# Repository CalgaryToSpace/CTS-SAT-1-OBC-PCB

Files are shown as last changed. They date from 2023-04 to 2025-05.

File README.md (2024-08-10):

# CTS-SAT-1-OBC-PCB

This is the design repository for the CTS-SAT-1 ("FrontierSat") onboard computer (OBC) PCB.

This OBC is host to an STM32 and several flash chips, and interfaces with all other electrical components on the 3U CubeSat.

## PCB Stackup

This PCB uses the [JLCPCB `JLC04161H-2116A` stackup](https://jlcpcb.com/impedance). It is a 6-layer, impedance-controlled PCB.

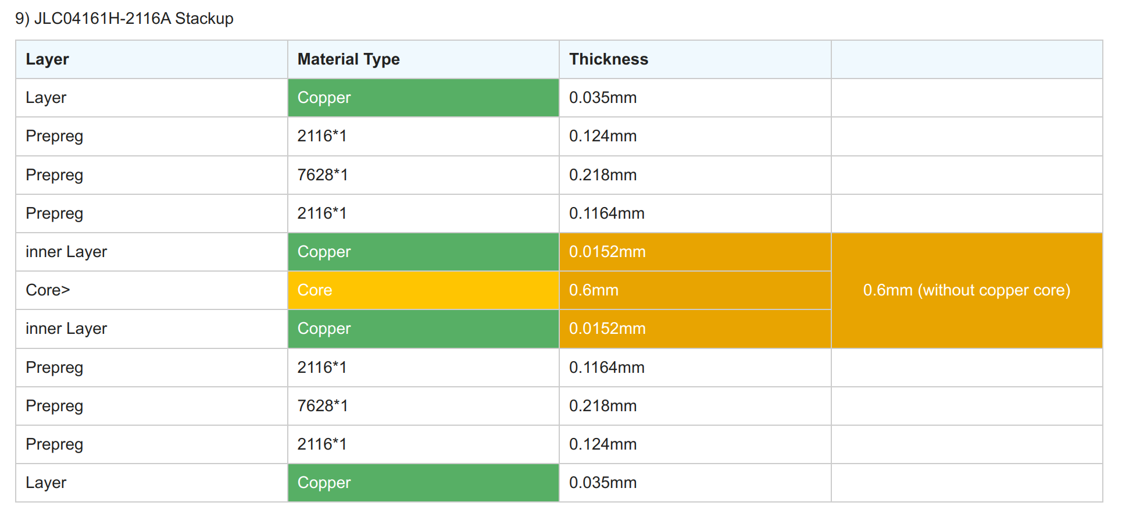
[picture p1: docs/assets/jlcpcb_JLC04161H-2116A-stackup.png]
JLC04161H-2116A Layer Stackup Table Screenshot


## Electrical Wire Comments

It is important to consider the outgassing characteristics of all wires used, so PTFE insulation has been chosen as the standard insulation material. The recommended part number is 5853 BK005, and the maximum recommended current is 1 amp per conductor.

If constructing Space Grade PCBs, use Rogers material as it has low outgassing properties.

## Repository Contents

* OBC PCB
* STM32CubeIDE Pinout/IOC configuration
* Unused early-stage umbilical connection board

## Contributors

* James Chen (contact chen.james2015@gmail.com with any questions)
* Others

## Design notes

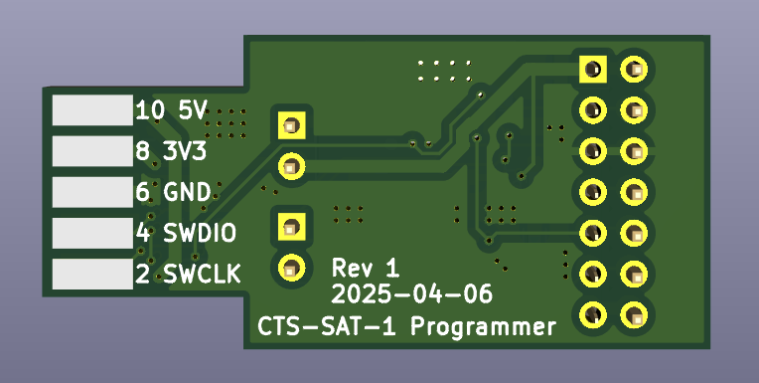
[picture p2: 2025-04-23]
Supplemental_PCBs/Programming_Connector_Adapter_PCB/Render_Bottom.png

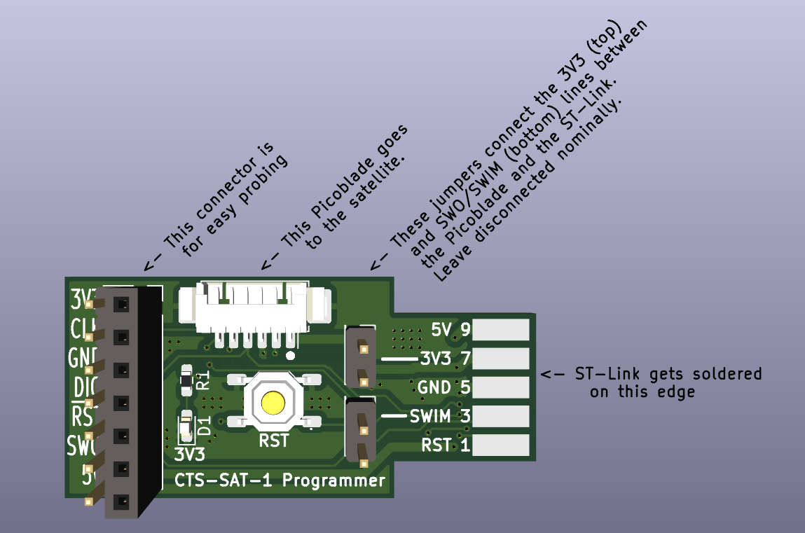
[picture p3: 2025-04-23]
Supplemental_PCBs/Programming_Connector_Adapter_PCB/Render_Top.png

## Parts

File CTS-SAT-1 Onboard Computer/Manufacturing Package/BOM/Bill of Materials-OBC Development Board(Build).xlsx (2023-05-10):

Designator | Description | Quantity | Distributor | Distributor Part # | Manufacturer | Manufacturer Part #
*1, *2, *3, *4 |  | 4
C1, C3, C4, C5, C6, C7, C8, C9, C10, C14, C15, C16, C17, C18, C19, C22, C23, C24, C25, C26, C27, C28, C29, C30, C32, C51, C53 | 0.1 µF ±10% 25V Ceramic Capacitor X7R 0603 (1608 Metric) | 27 | Digikey | 1276-1006-1-ND | Samsung Electro-Mechanics | CL10B104KA8NNNC
C2, C31 | CAP CER 1UF 25V X7R 0603 | 2 | Digikey | 311-1802-1-ND | Yageo | CC0603KRX7R8BB105
C11, C13, C48, C49, C50 | 4.7 µF Molded Tantalum Capacitors 20 V 1206 (3216 Metric) 4Ohm | 5 | Digikey | 478-1668-1-ND | AVX Corporation | TAJA475K020RNJ
C12, C20 | CAP CER 0.1UF 25V X7R 0402 | 2 | Digikey | 13-CC0402KPX7R8BB104CT-ND | YAGEO | CC0402KPX7R8BB104
C21 | 15 pF ±1% 50V Ceramic Capacitor C0G, NP0 0402 (1005 Metric) | 1 | Digikey | 311-1642-1-ND | YAGEO | CC0402FRNPO9BN150
C33 | CAP TANT 22UF 10% 10V 1206 | 1 | Digikey | 478-11193-1-ND | KYOCERA AVX | TPSA226K010T0900
C34, C35, C36 | CAP ALUM POLY 47UF 20% 25V SMD | 3 | Digikey | P16513CT-ND | Panasonic Electronic Components | 25SVPF47M
C39, C44 | CAP CER 4.7UF 16V X7R 0603 | 2 | Digikey | 490-GRM188Z71C475KE21JCT-ND | Murata Electronics | GRM188Z71C475KE21J
C42, C45, C47 | CAP CER 100PF 50V X7R 0603 | 3 | Digikey | 311-3601-1-ND | YAGEO | CC0603KRX7R9BB101
C43, C46 | CAP CER 33PF 50V X7R 0603 | 2 | Digikey | 399-C0603C330K5RAC7867CT-ND | KEMET | C0603C330K5RAC7867
C52 | CAP CER 10000PF 50V X7R 0603 | 1 | Digikey | 1276-1009-1-ND | Samsung Electro-Mechanics | CL10B103KB8NNNC
D1, D2, D3, D4, D5, D6 | Red 620nm LED Indication - Discrete 2.2V 0603 _1608 Metric | 6 | Digikey | SML-D12U1WT86CT-ND | Rohm Semiconductor | SML-D12U1WT86
D7 | DIODE SCHOTTKY 40V 5A SMC | 1 | Digikey | B540C-FDICT-ND | Diodes Incorporated | B540C-13-F
J3, J8 | CONN HEADER SMD R/A 8POS 1.25MM | 2 | Digi-Key | WM7626CT-ND
J4 | CONN HEADER SMD R/A 4POS 1.25MM | 1 | Digi-Key | WM7622CT-ND
J5, J6 | CONN SOCKET 52POS 0.1 GOLD PCB | 2 | Digikey | SAM11114-ND | Samtec Inc. | ESQ-126-14-G-D
J7, J9, J11 | CONN HEADER SMD R/A 6POS 1.25MM | 3 | Digi-Key | WM7624CT-ND
J10, J13 | CONN HEADER VERT 10POS 1.25MM | 2 | Digikey | WM1739-ND | Molex | 0530471010
J12 | Connector Header Surface Mount, Right Angle 14 position 0.049 (1.25mm) | 1 | Digikey | 900-0532617014CT-ND | Molex | 0532617014
J14, J16, J17, J18, J20 | CONN MCX RCPT STR 50 OHM PCB | 5 | Digikey | ACX1262-ND | Amphenol RF | 252105
L1 | FIXED IND 6.8UH 8A 23.3 MOHM SMD | 1 | Digikey | 541-1303-1-ND | Vishay Dale | IHLP4040DZER6R8M01
R1, R2, R3 | 220 Ohms ±0.5% 0.063W, 1/16W Chip Resistor 0603 (1608 Metric) - Thin Film | 3 | Digikey | RR08P220DCT-ND | Susumu | RR0816P-221-D
R4, R5, R6, R7, R13, R14, R15, R16, R17, R22, R24, R26, R27, R28, R30, R31, R32, R33, R34, R35, R36, R37, R38, R41, R42, R43, R44, R45, R46, R47, R51, R52, R53, R55, R63, R64, R67 | 0 Ohms Jumper 0.1W, 1/10W Chip Resistor 0603 (1608 Metric) Automotive AEC-Q200 Thick Film | 37 | Digikey | RMCF0603ZT0R00CT-ND | Stackpole Electronics Inc | RMCF0603ZT0R00
R8, R11 | RES SMD 1K OHM 1% 1/16W 0603 | 2 | Digikey | A102226CT-ND | TE Connectivity Passive Product | CPF0603F1K0C1
R9, R10, R12, R18, R21, R23, R25, R29, R39, R40, R48, R50, R56, R57, R58, R59, R107, R109 | 22 Ohms ±0.5% 0.063W, 1/16W Chip Resistor 0603 (1608 Metric) - Thin Film | 18 | Digikey | RR08Q22DCT-ND | Susumu | RR0816Q-220-D
R19, R20, R49, R54, R91, R92 | RES SMD 4.7K OHM 1% 1/10W 0603 | 6 | Digikey | CR0603-FX-4701ELFCT-ND | Bourns Inc. | CR0603-FX-4701ELF
R60, R61, R65, R66, R117, R118, R119, R120, R124, R125, R126, R127, R128, R129, R136 | RES 10K OHM 1% 1/8W 0603, 10 kOhms ±0.1% 0.063W, 1/16W Chip Resistor 0603 (1608 Metric) - Thin Film | 15 | Digikey | RNCP0603FTD10K0CT-ND, A119886CT-ND | Stackpole Electronics Inc, TE Connectivity Passive Product | RNCP0603FTD10K0, CPF0603B10KE
R62 | RES 0.5 OHM 1% 1W 2010 | 1 | Digikey | 541-10112-1-ND | Vishay Dale | WSLT2010R5000FEA18
R130, R131 | RES SMD 100 OHM 0.5% 1/16W 0603 | 2 | Digikey | RR08P100DCT-ND | Susumu | RR08P100DCT-ND
R134, R135 | RES 220 OHM 5% 1/16W 0402 | 2 | Digikey | 311-220JRCT-ND | Yageo | RC0402JR-07220RL
TP1, TP2 | Test Point | 2
U1 | IC MCU 32BIT 2MB FLASH 144LQFP | 1 | Mouser |  | STMicroelectronics | STM32L4R5ZIT6
U2, U3, U5, U6 | IC FLASH 1GBIT SPI/QUAD 16SOIC | 4 | Digikey | 1274-1092-ND | Cypress Semiconductor | S70FL01GSAGMFI011
U4 | IC REG BUCK ADJUSTABLE 3A 8SOIC | 1 | Digikey | 505-ADP2303ARDZ-ND | Analog Devices Inc. | ADP2303ARDZ
U7, U8 | IC FRAM 8MBIT SPI 40MHZ 8GQFN | 2 | Digikey | 428-4723-ND | Cypress Semiconductor | CY15B108QN-40LPXI
U9 | IC TRNSLTR BIDIRECTIONAL 14TSSOP | 1 | Digikey | MAX3378EEUD+TCT-ND | Maxim Integrated | MAX3378EEUD+T
U10 | IC TRANSCEIVER FULL 1/1 14SOIC | 1 | Digikey | MAX3086EESD+TCT-ND | Maxim Integrated Products | MAX3086EESD+T
U11, U12 | LORA-E5 WIRELESS MODULE (TAPE RE | 2 | Digikey | 1597-317990829CT-ND | Seeed Technology Co., Ltd | 317990829
U13 | IC RF SWITCH SPDT 3GHZ 6MLPD | 1 | Digikey |  | Skyworks Solutions Inc. | SKY13323-378LF
U14 | IC INVERT SCHMITT 1CH 1IN SC70 | 1 | Digikey
Y1 | XTAL OSC TCXO 20.0000MHZ CSWV | 1 | Digikey | 114-TG2520SMN20.0000M-MCGNNM3CT-ND | EPSON | TG2520SMN 20.0000M-MCGNNM3
Y2 | XTAL OSC TCXO 32.7680KHZ CMOS | 1 | Digikey | SER4422CT-ND | EPSON | TG-3541CE 32.7680KXB3

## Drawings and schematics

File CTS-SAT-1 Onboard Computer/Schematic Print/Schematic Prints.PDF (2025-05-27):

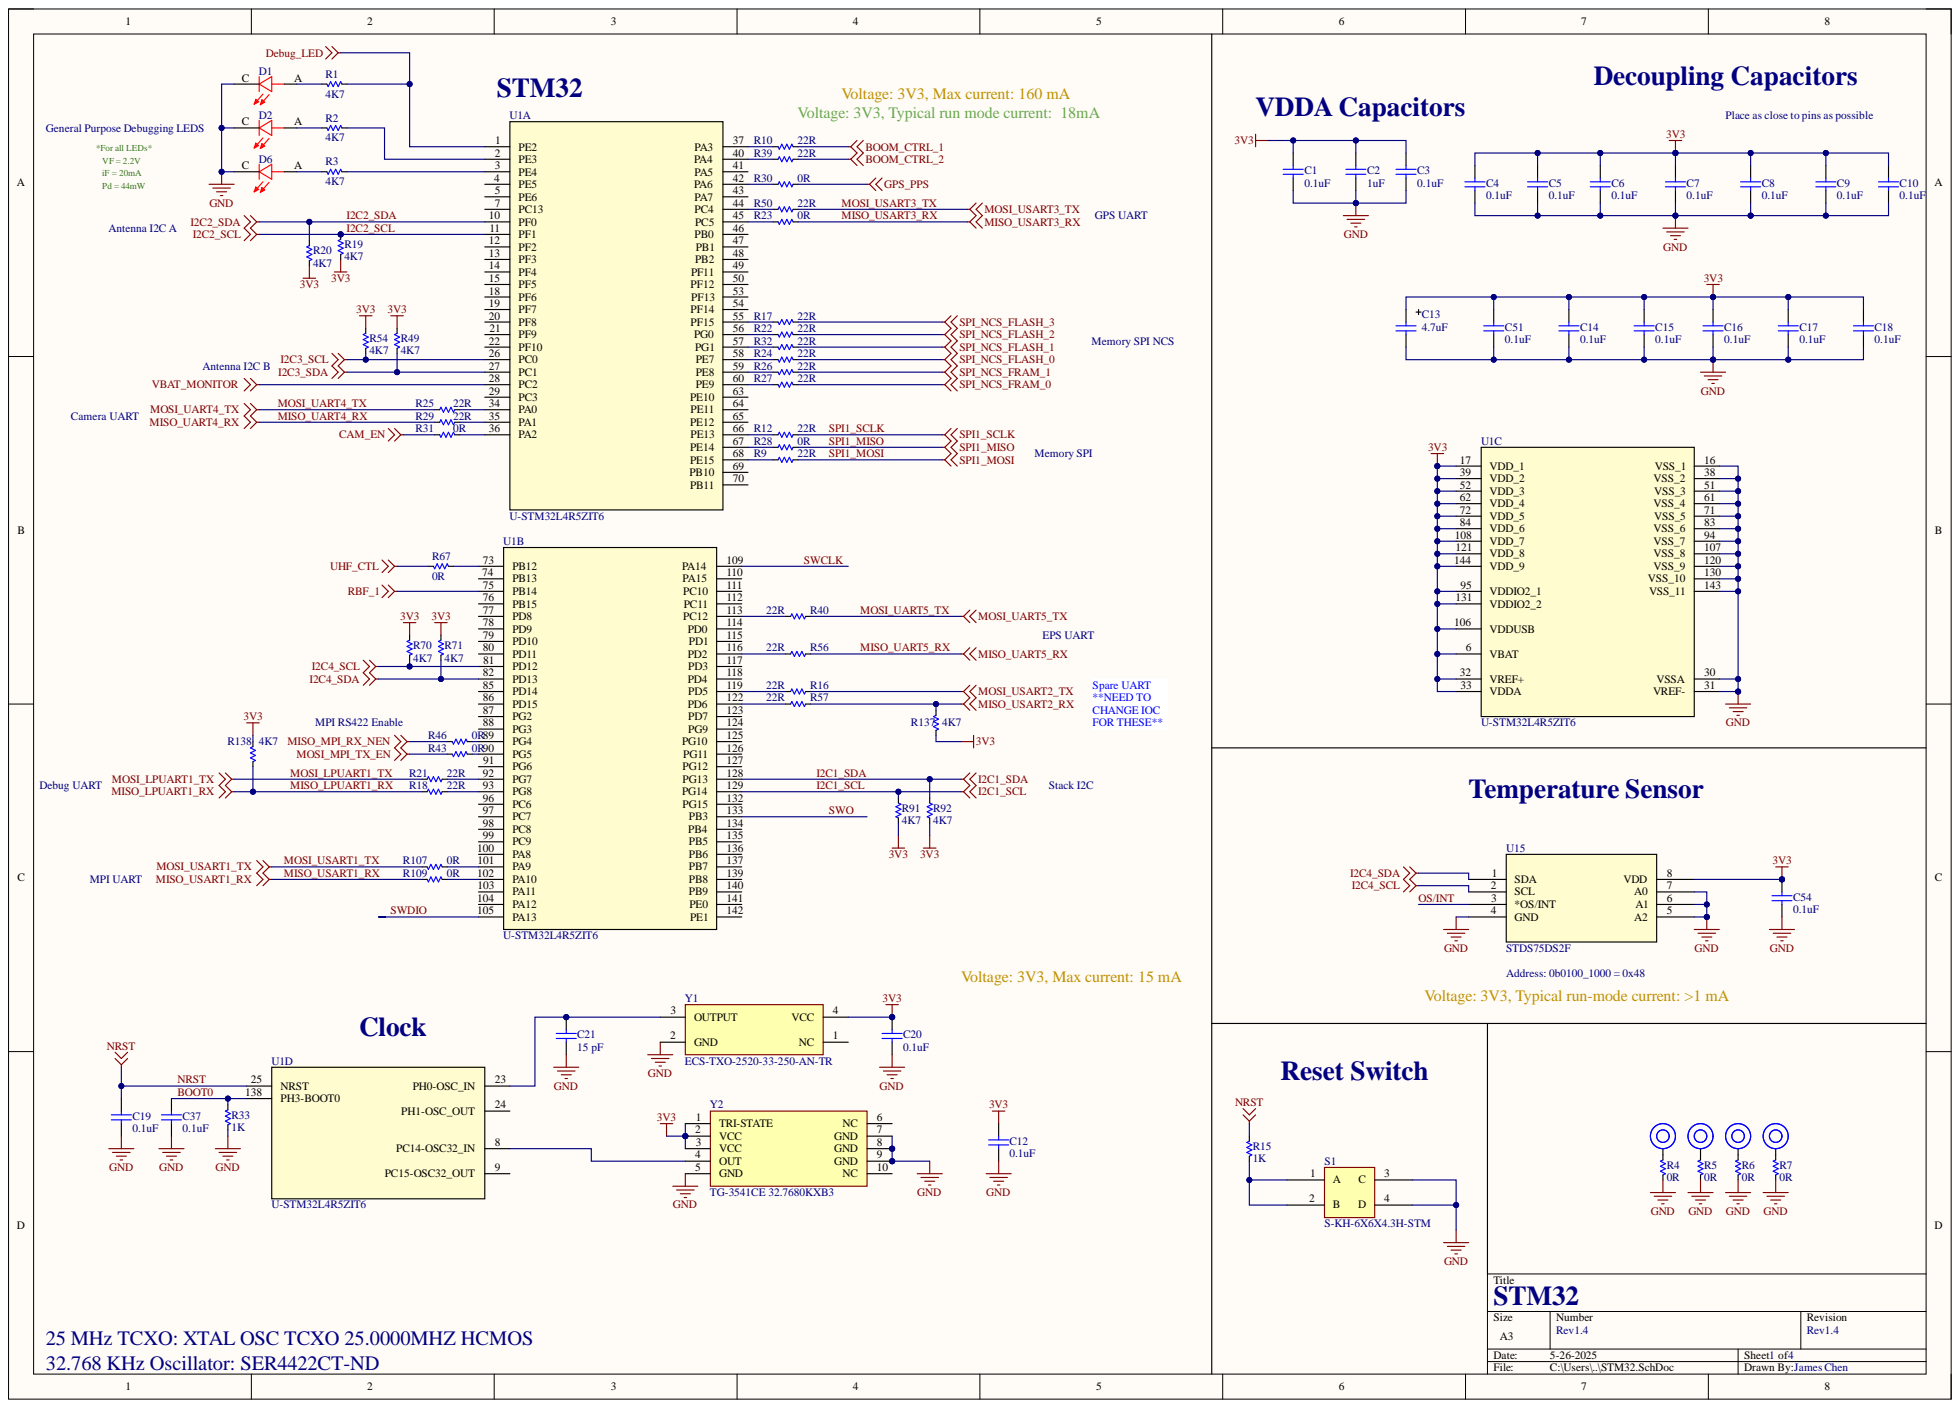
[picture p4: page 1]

Voltage: 3V3, Max current: 160 mA

Voltage: 3V3, Typical run mode current: 18mA

General Purpose Debugging LEDS

Voltage: 3V3, Max current: 15 mA

Voltage: 3V3, Typical run-mode current: >1 mA

ECS-TXO-2520-33-250-AN-TR

BOOT0 | PH3-BOOT0 138

25 MHz TCXO: XTAL OSC TCXO 25.0000MHZ HCMOS
32.768 KHz Oscillator: SER4422CT-ND

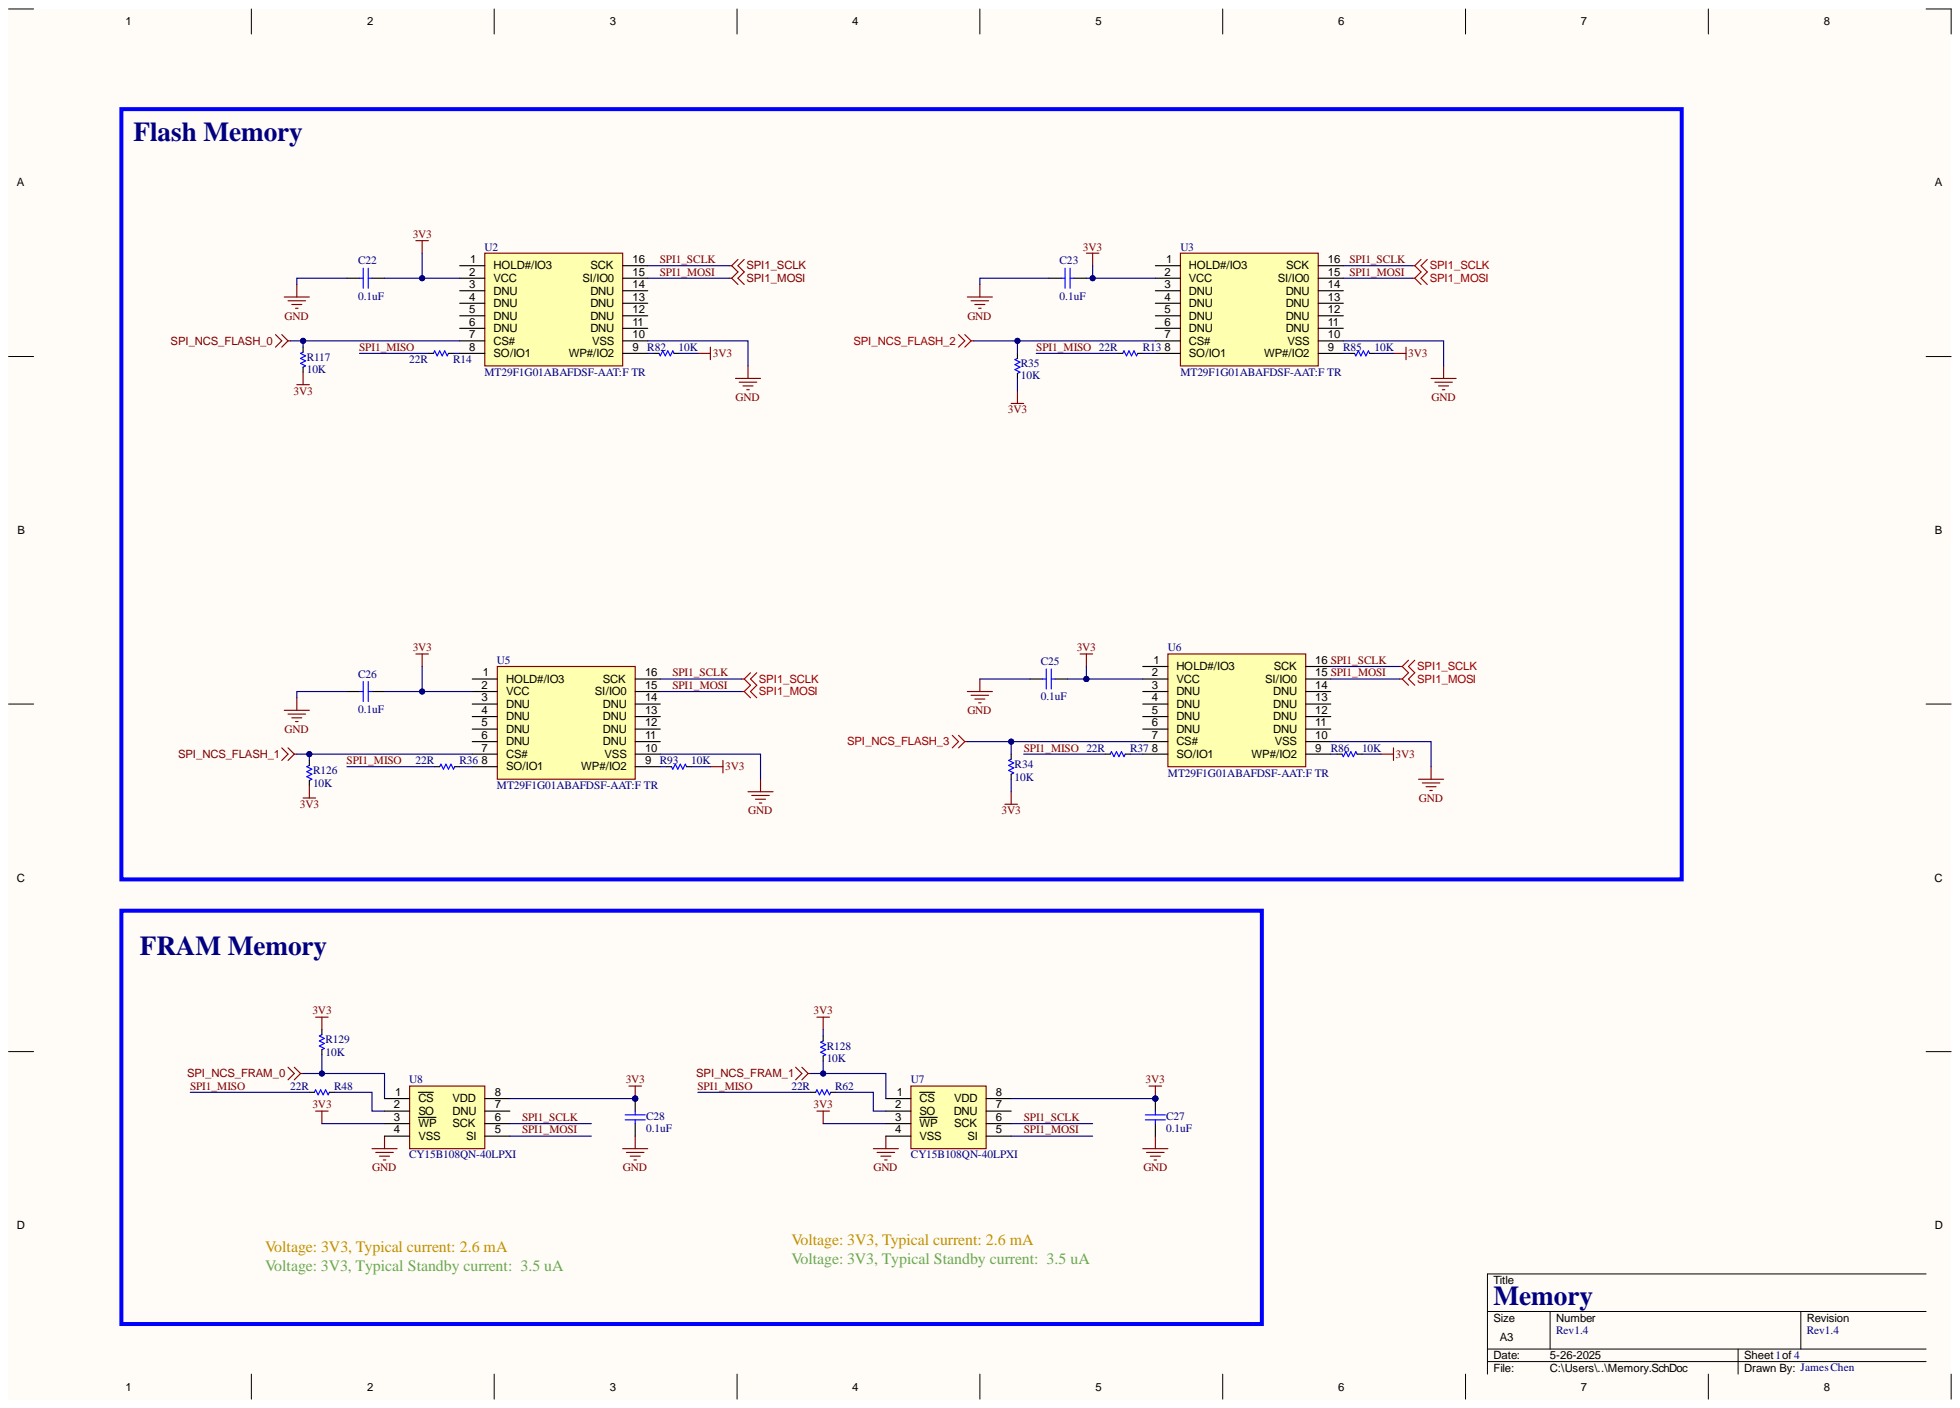
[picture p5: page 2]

Voltage: 3V3, Typical current: 2.6 mA
Voltage: 3V3, Typical Standby current: 3.5 uA

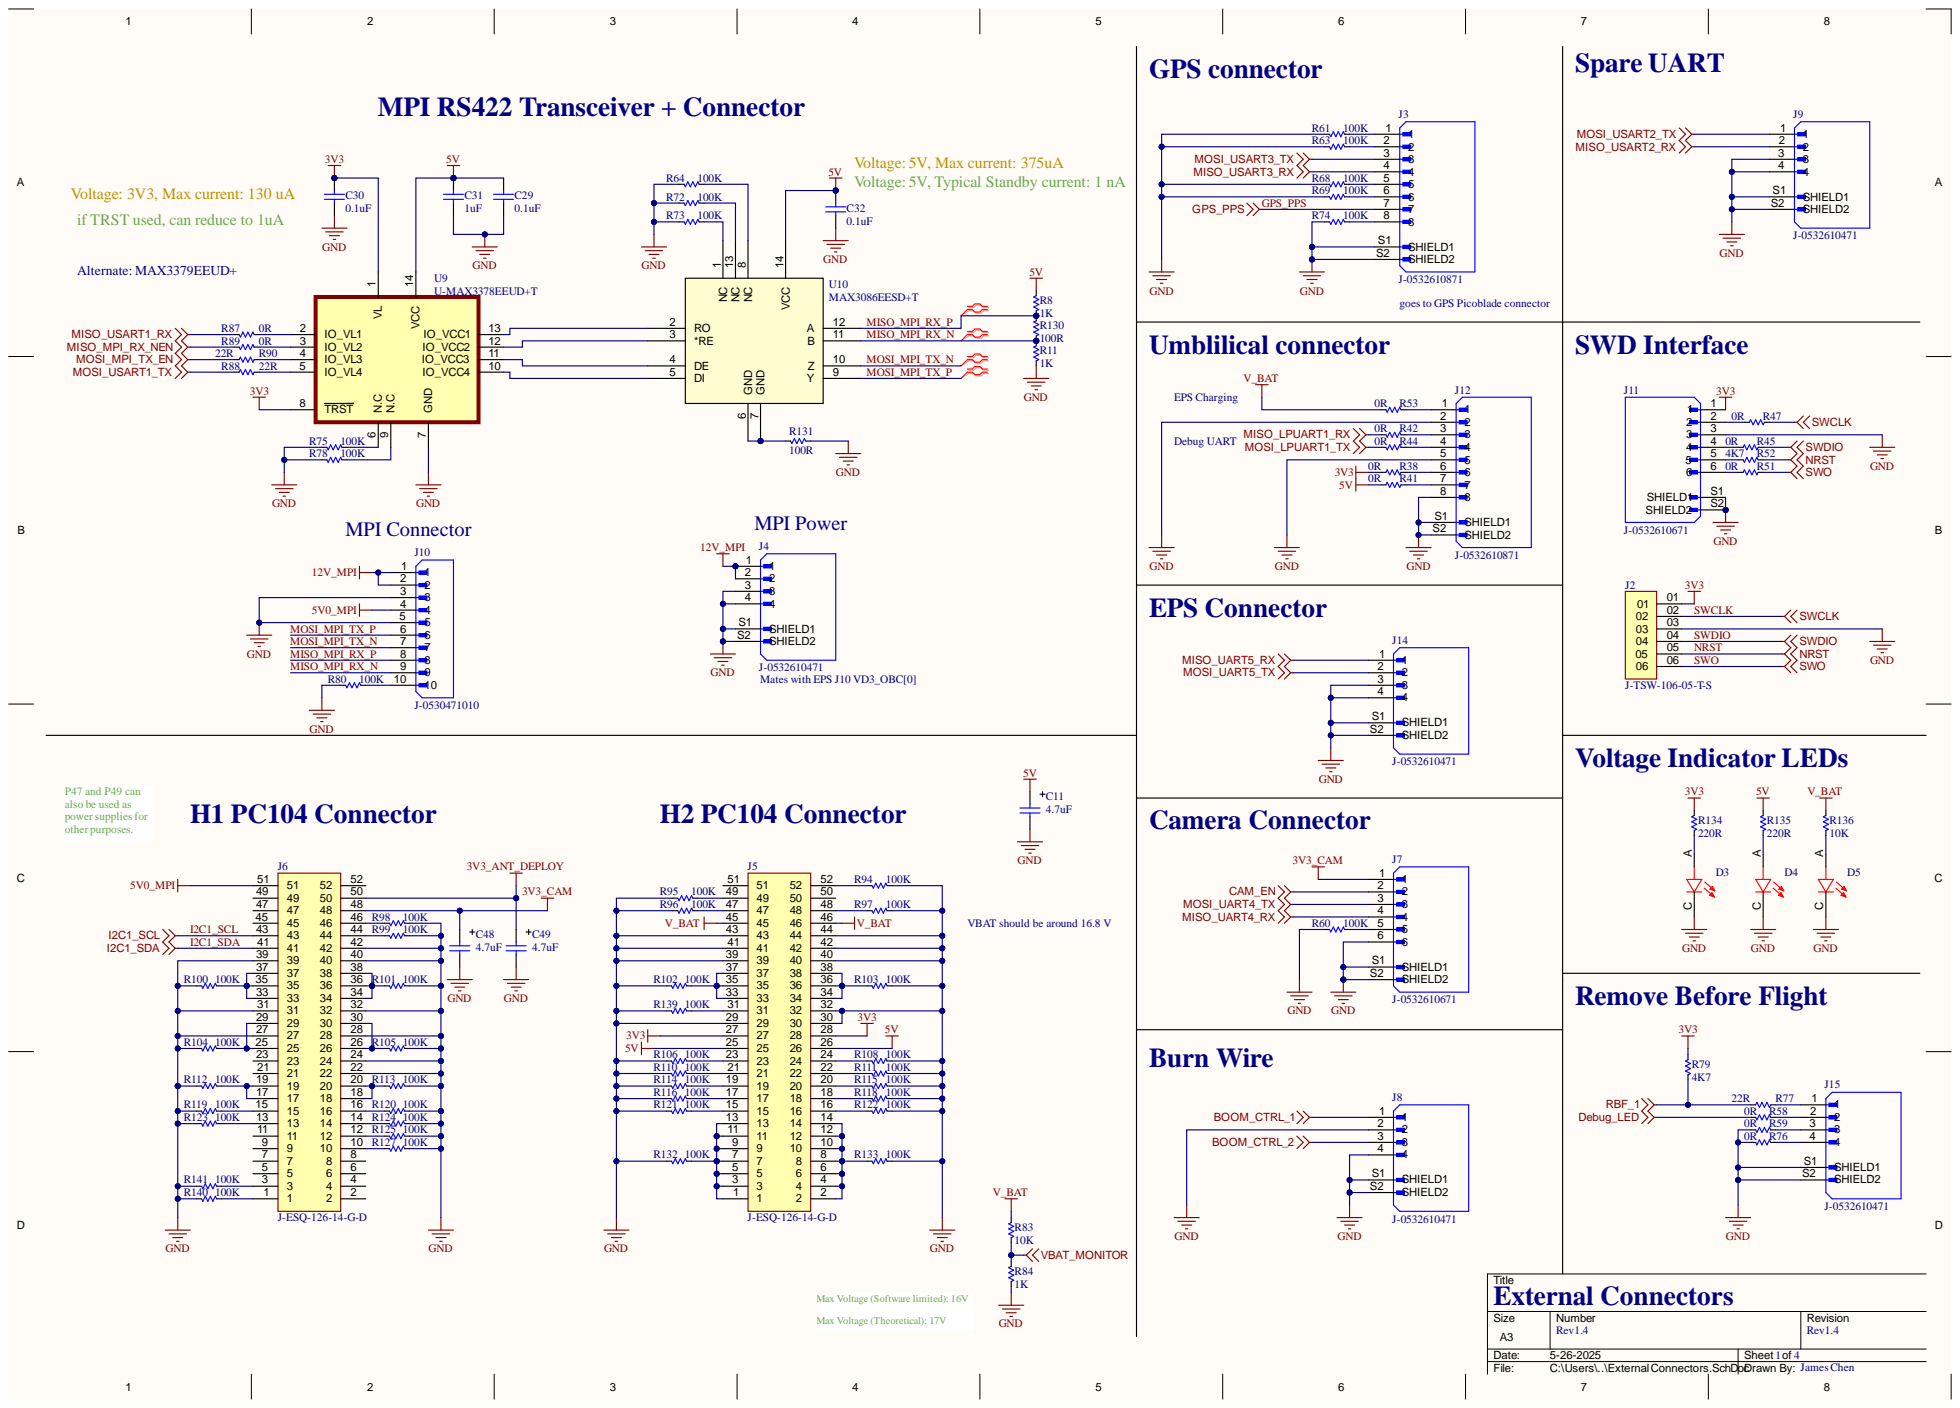
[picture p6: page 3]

0R R38 | 6
0R R41 | 7

S 1
S 2

so be used as
suppl

AT should be around 16.8 V

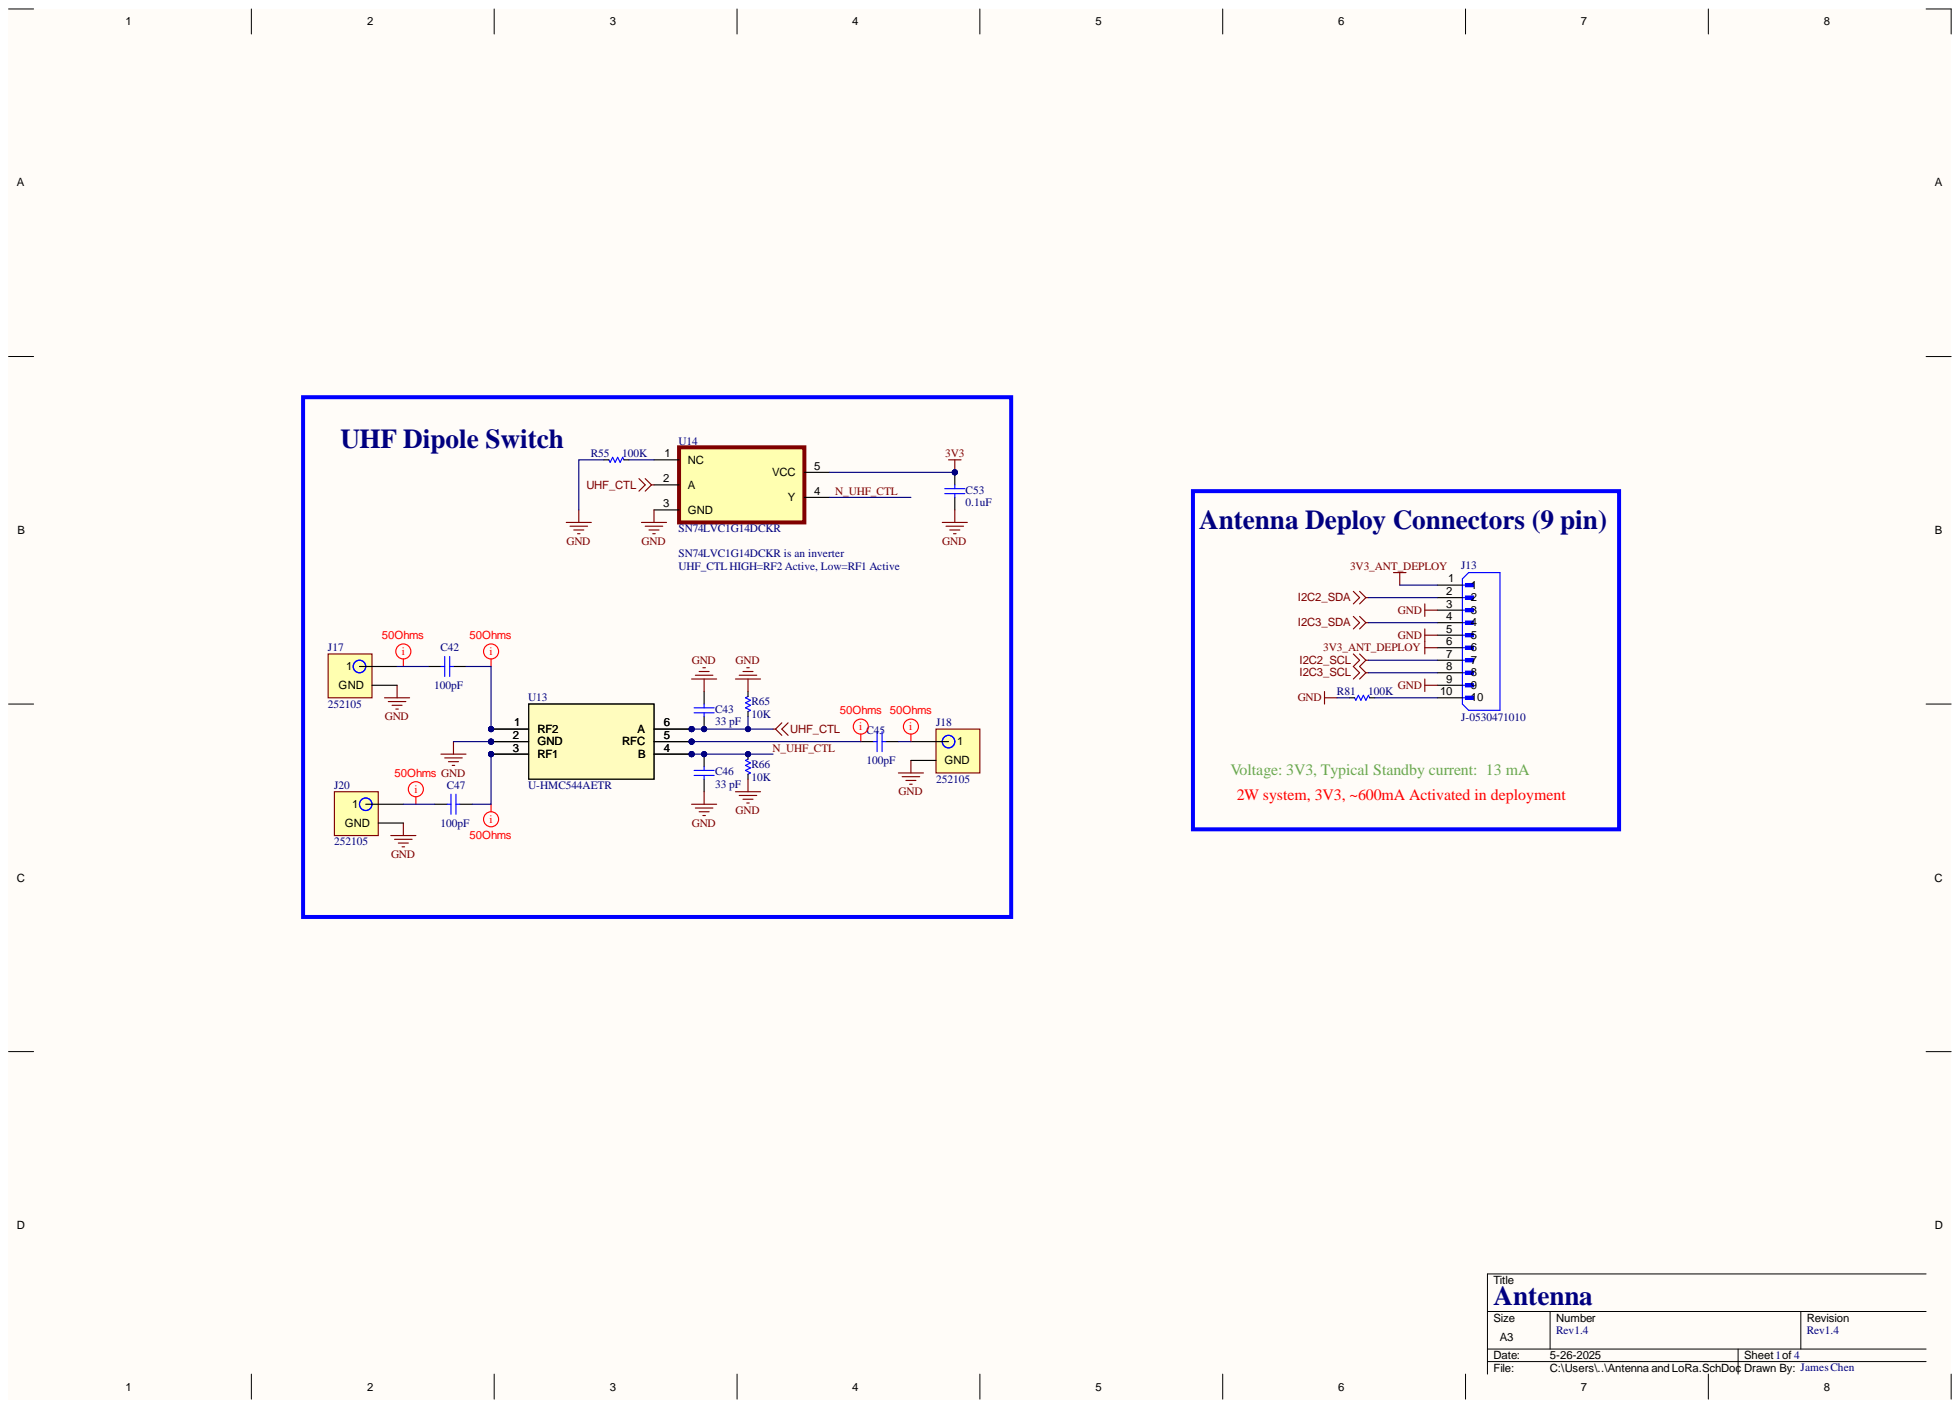
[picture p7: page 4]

UHF Dipole Switch GNDGND

Antenna Deploy Connectors (9 pin) Voltage: 3V3, Typical Standby current: 13 mA

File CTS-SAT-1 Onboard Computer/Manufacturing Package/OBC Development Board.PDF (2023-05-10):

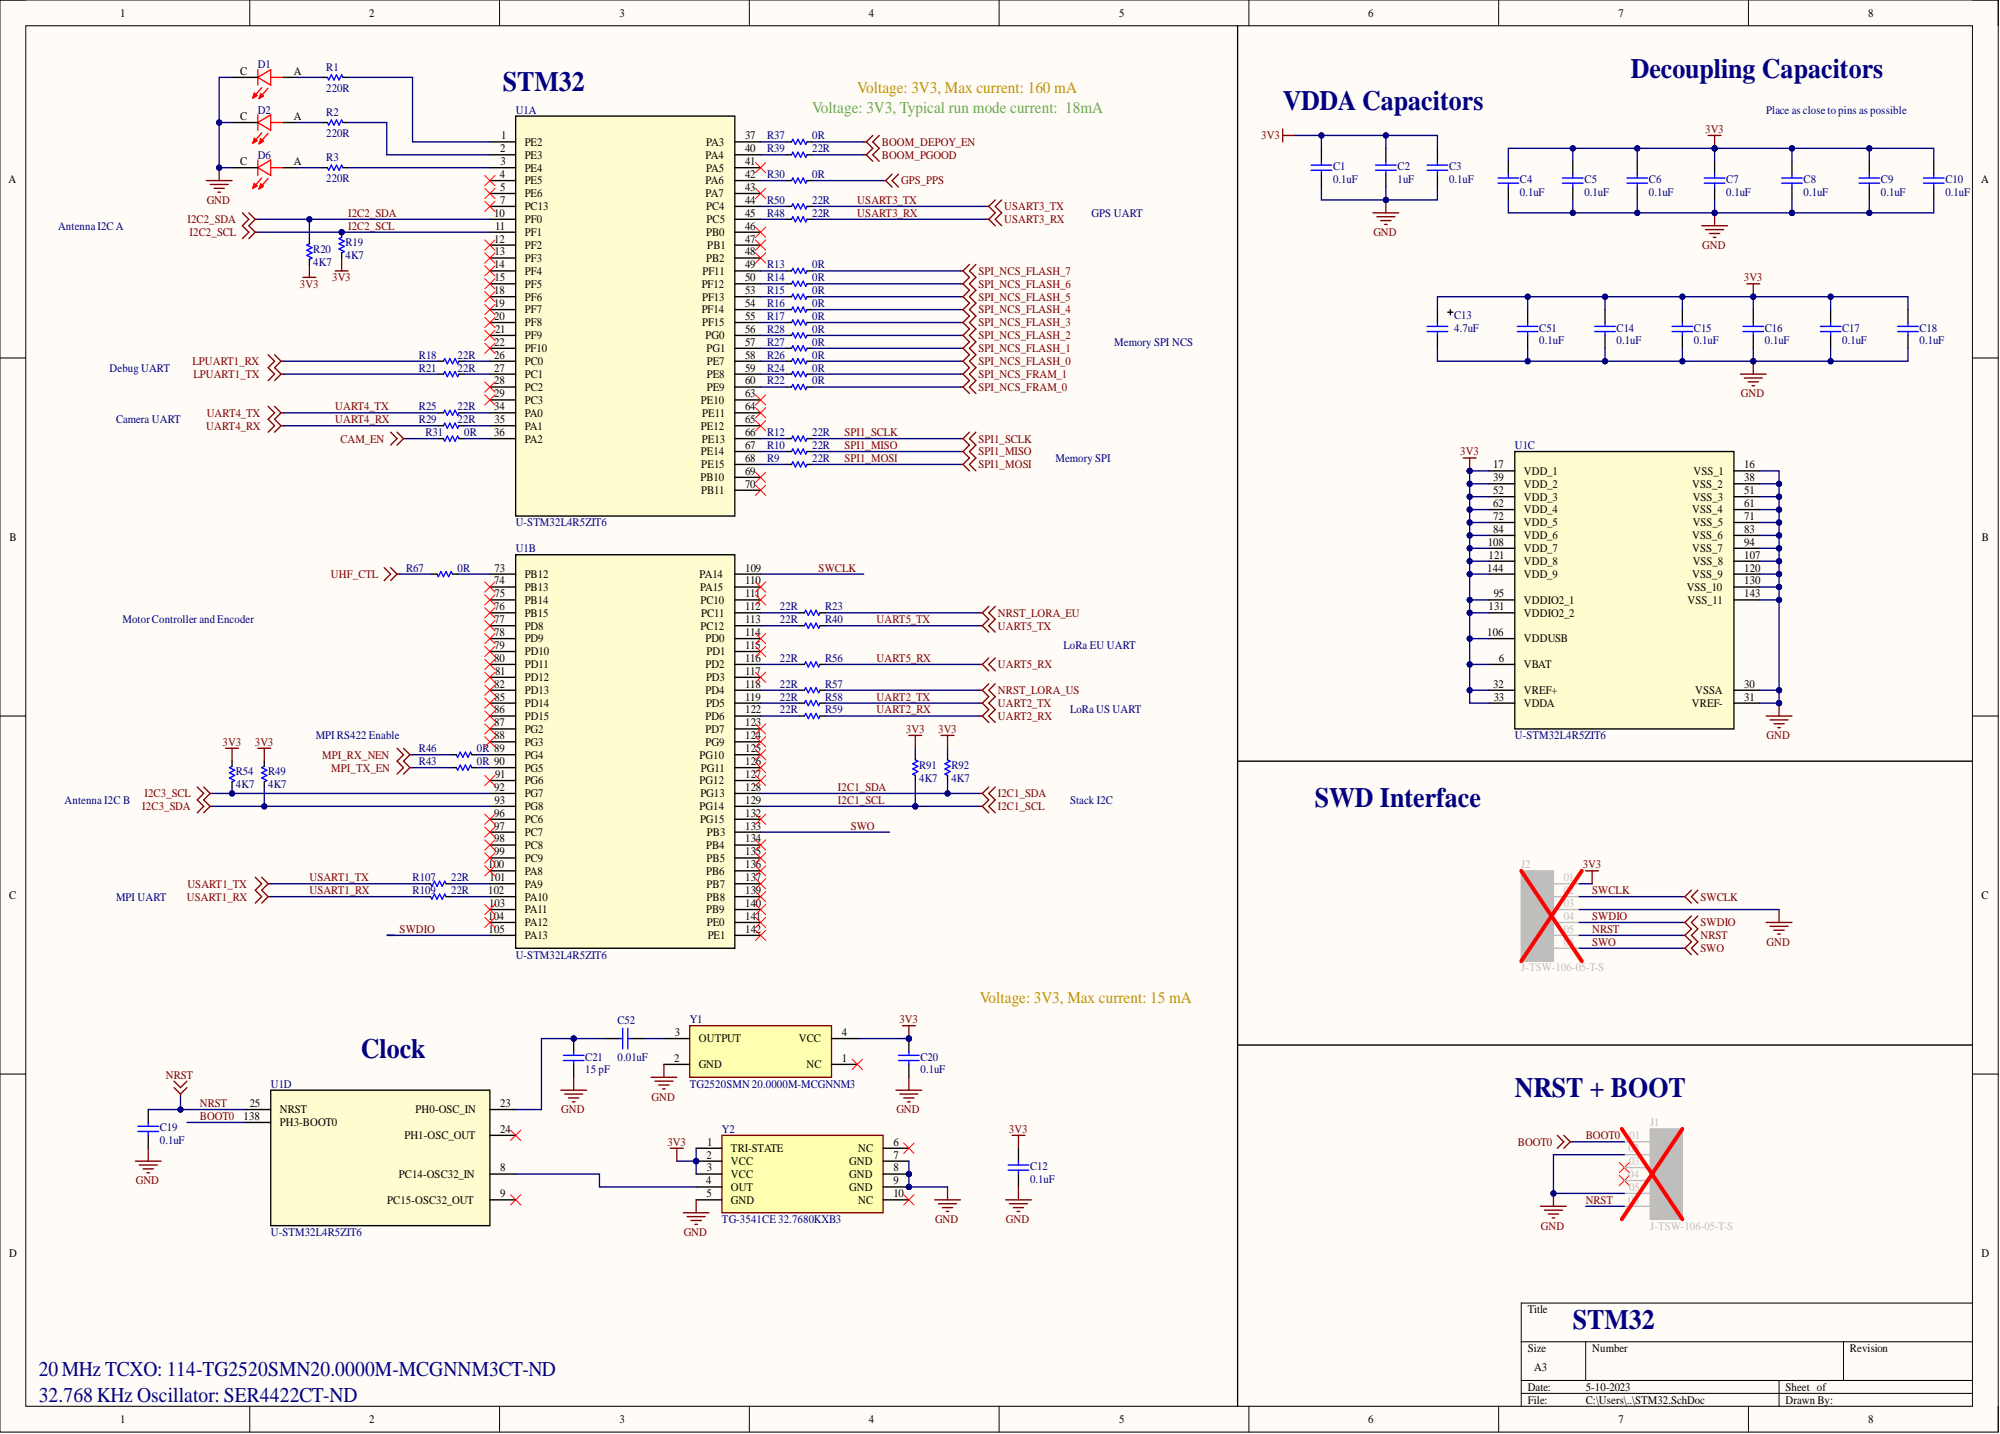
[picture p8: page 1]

3 9 | 3 8
5 2 | 5 1
6 2 | 6 1
7 2 | 7 1
8 4 | 8 3
1 0 8 | 9 4
1 2 1 | 1 0 7
1 4 4 | 1 2 0
9 5 | 1 3 0

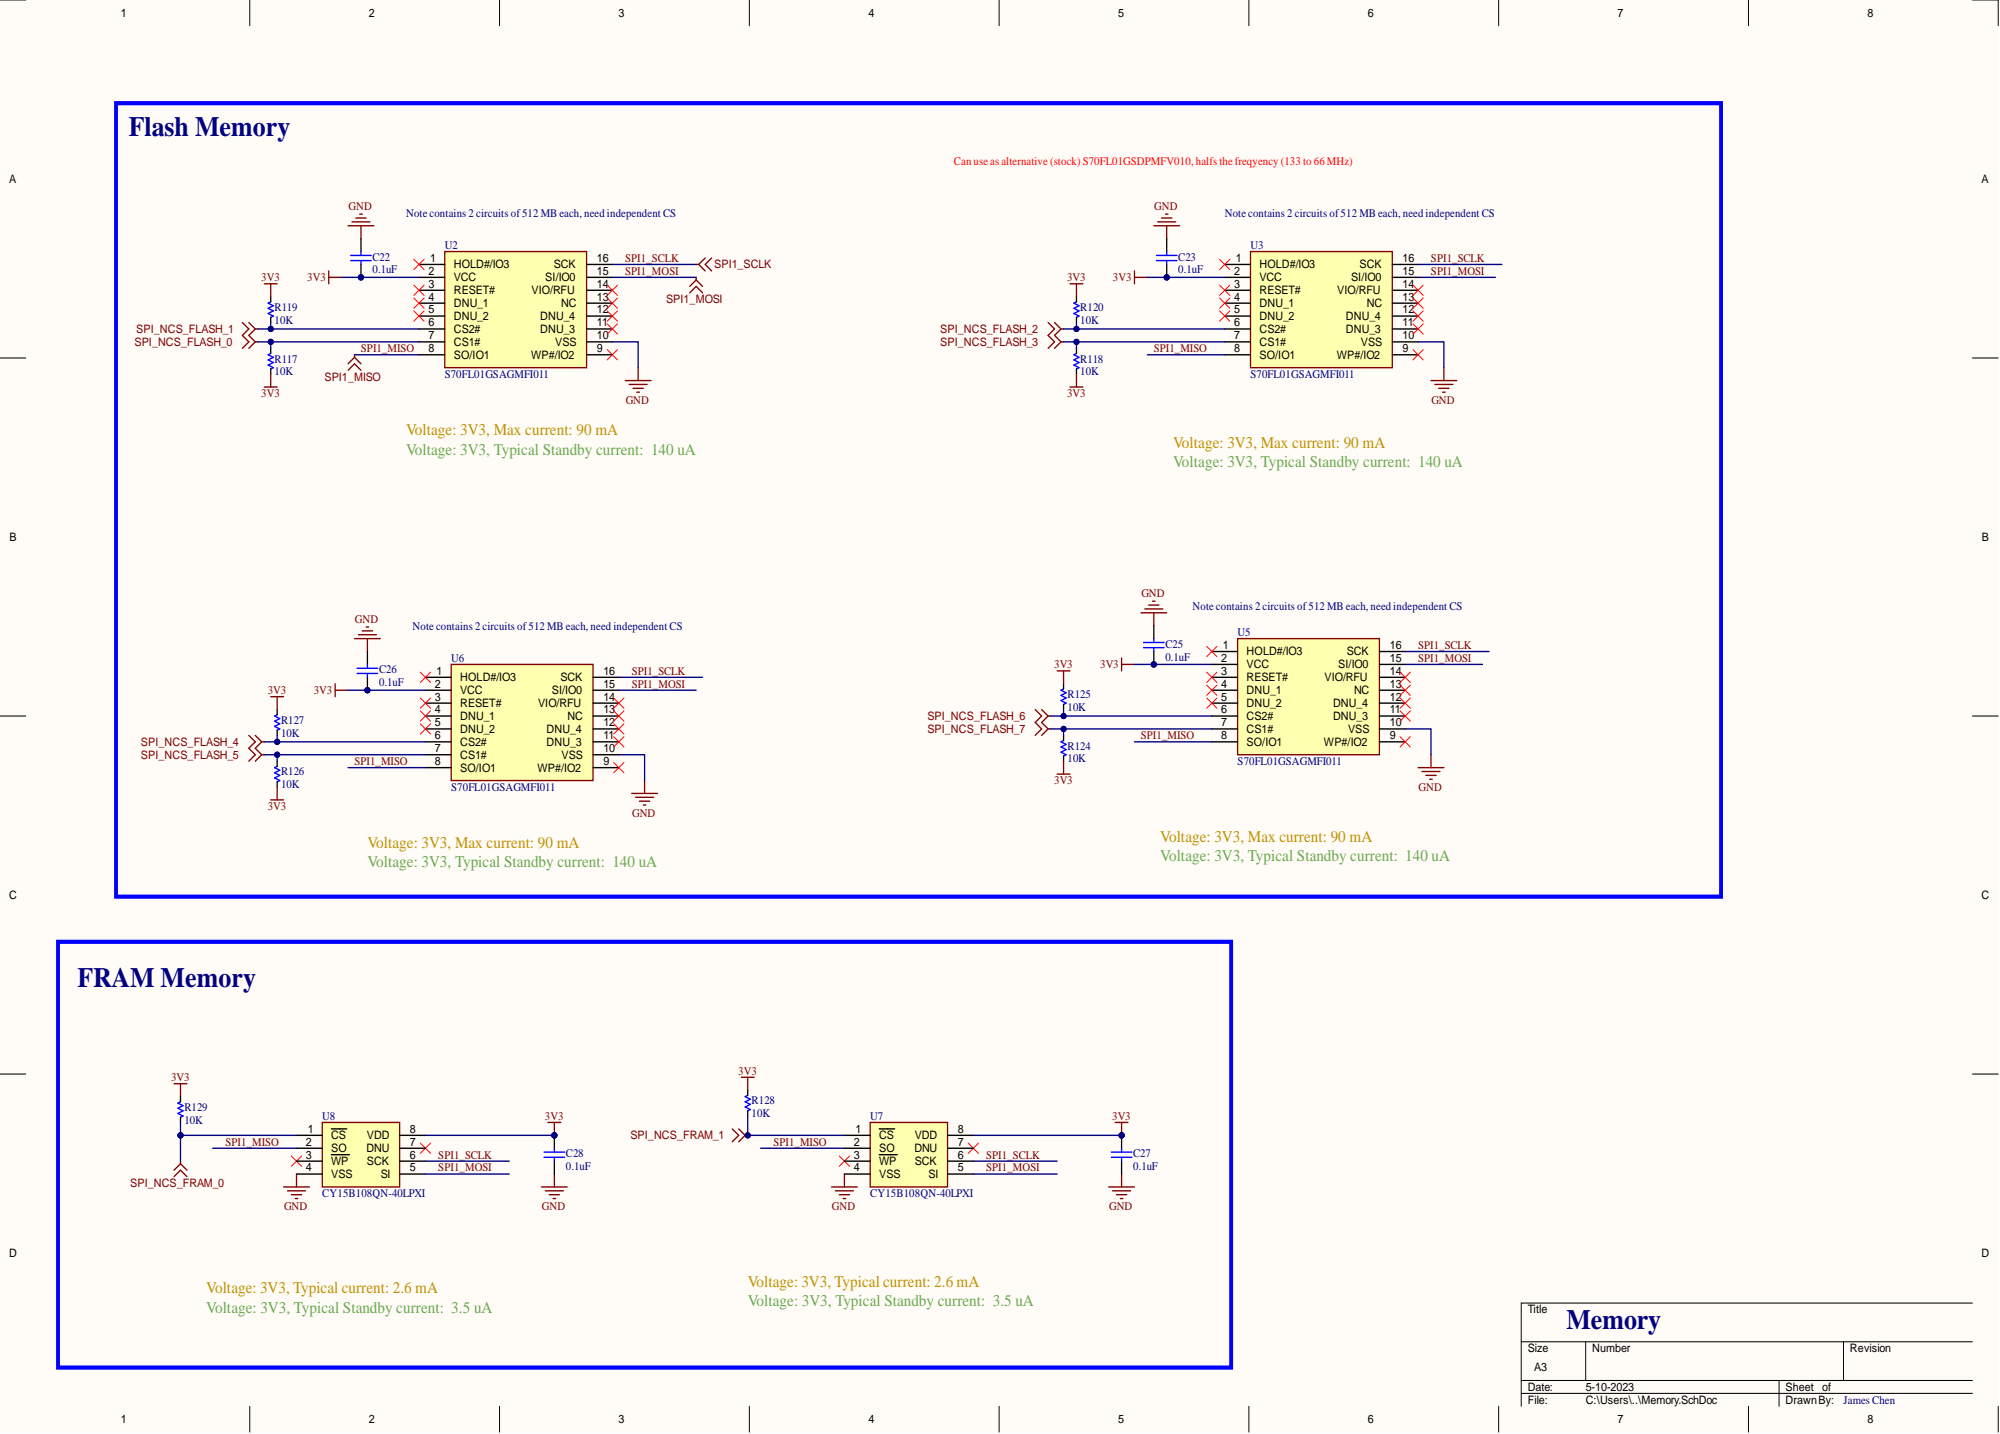
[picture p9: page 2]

Can use as alternative (stock) S70FL01GSDPMFV010, halfsthe freqyency (133 to 66 MHz)

Note contains 2 circuits of 512 MB each, need independent CS

Voltage: 3V3, Max current: 90 mA

Voltage: 3V3, Typical Standby current: 140 uA

Voltage: 3V3, Typical current: 2.6 mA
Voltage: 3V3, Typical Standby current: 3.5 uA

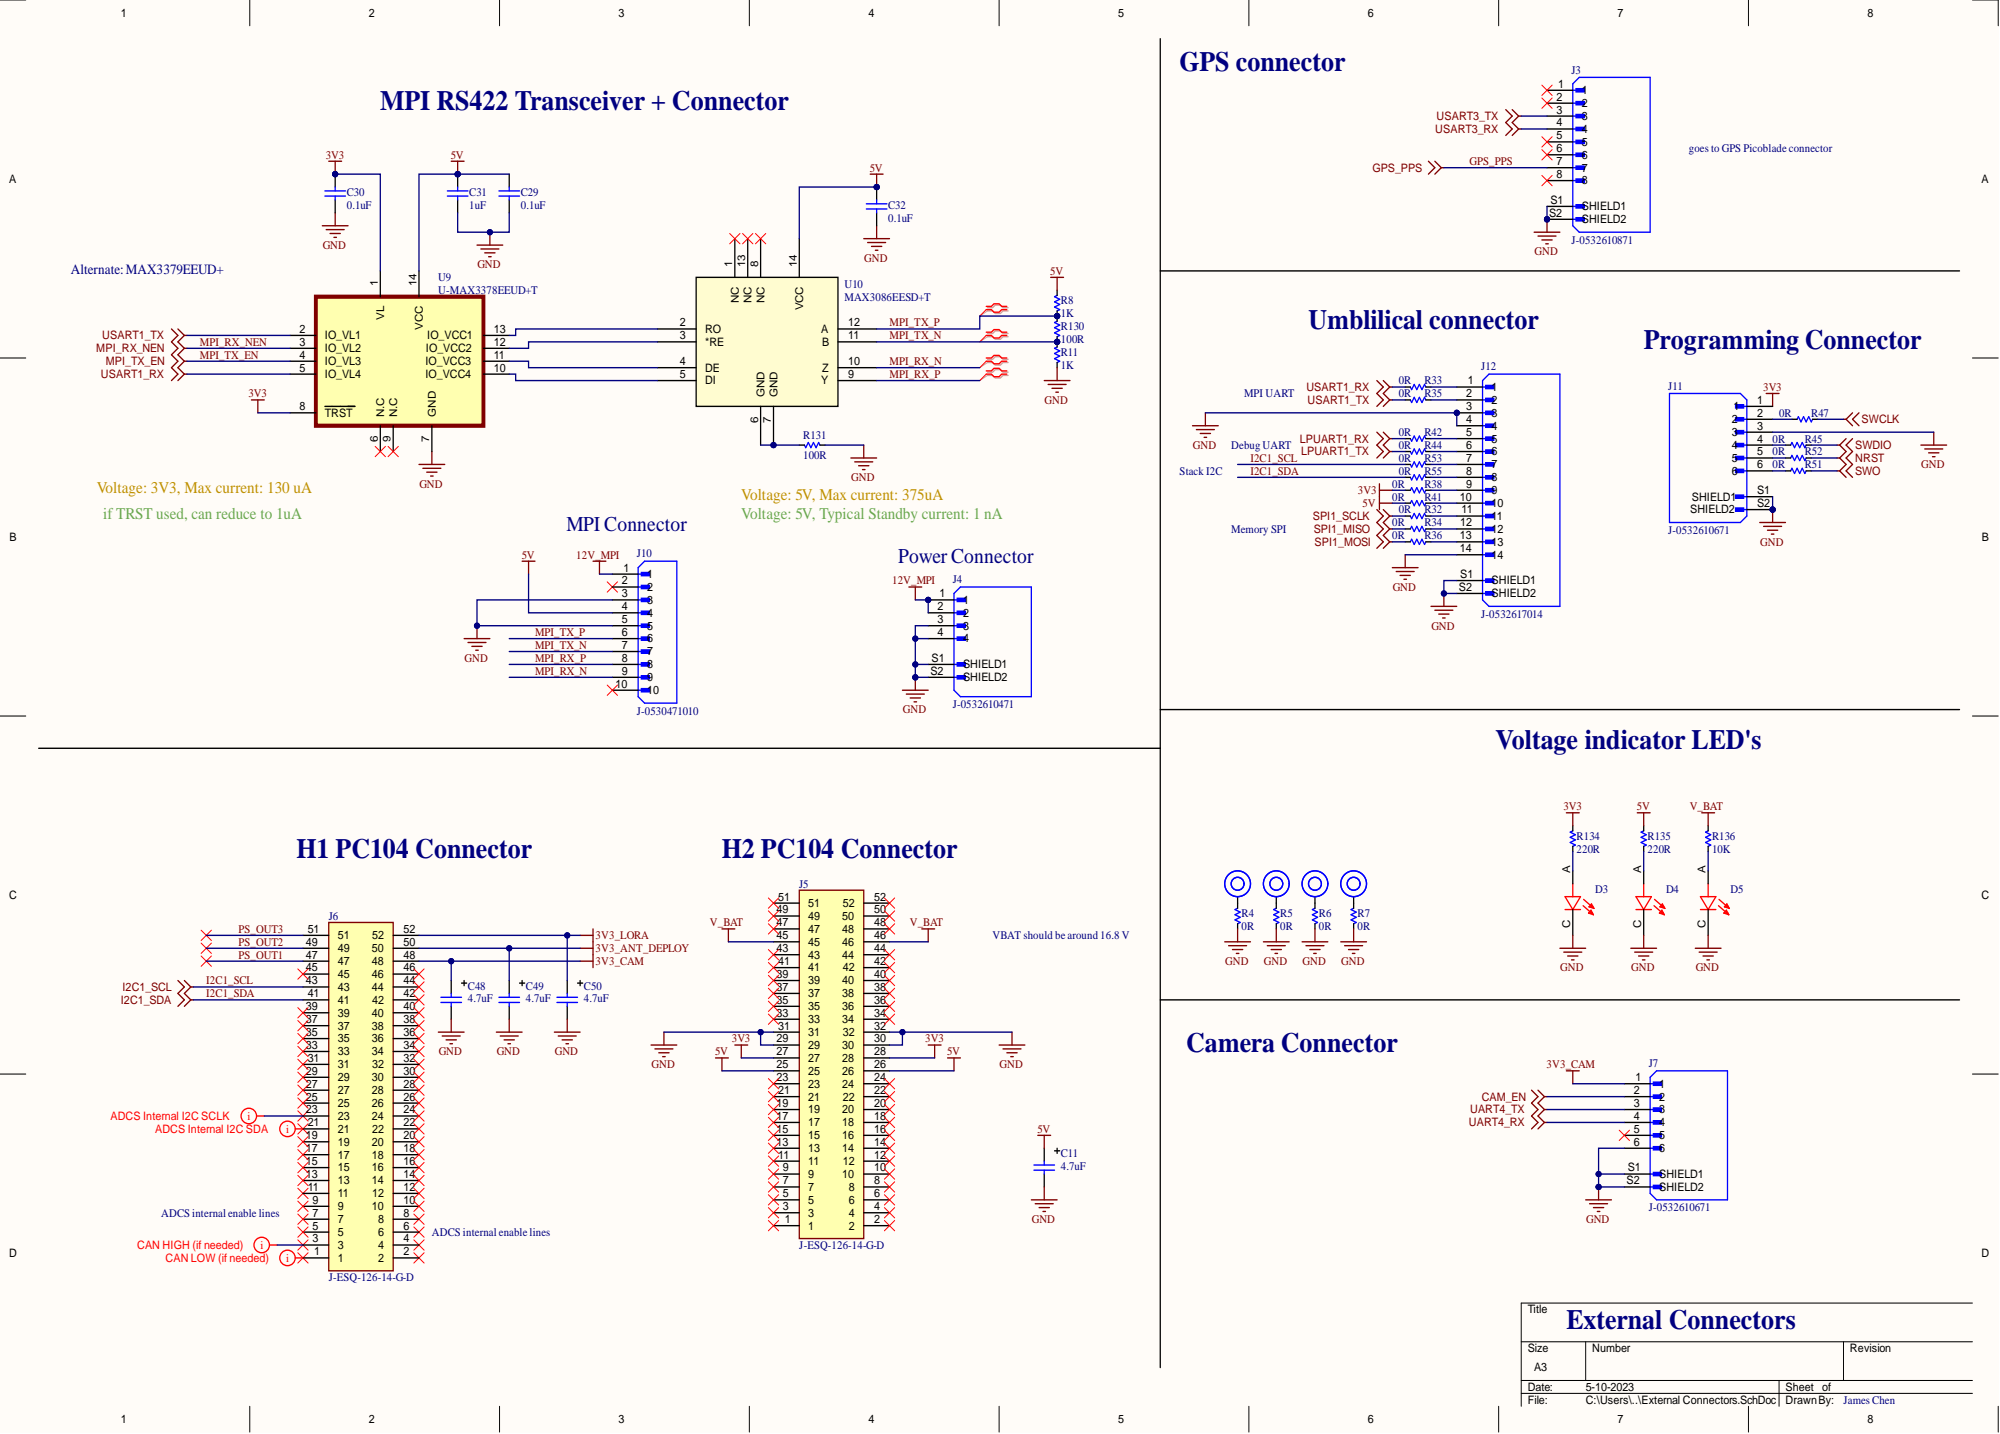
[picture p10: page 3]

goes to GPS Picoblade connector

Voltage: 3V3, Max current: 130 uA
if TRST used, can reduce to 1uA

Voltage: 5V, Max current: 375uA
Voltage: 5V, Typical Standby current: 1 nA

VBAT should be around 16.8 V

ADCS internal enable lines

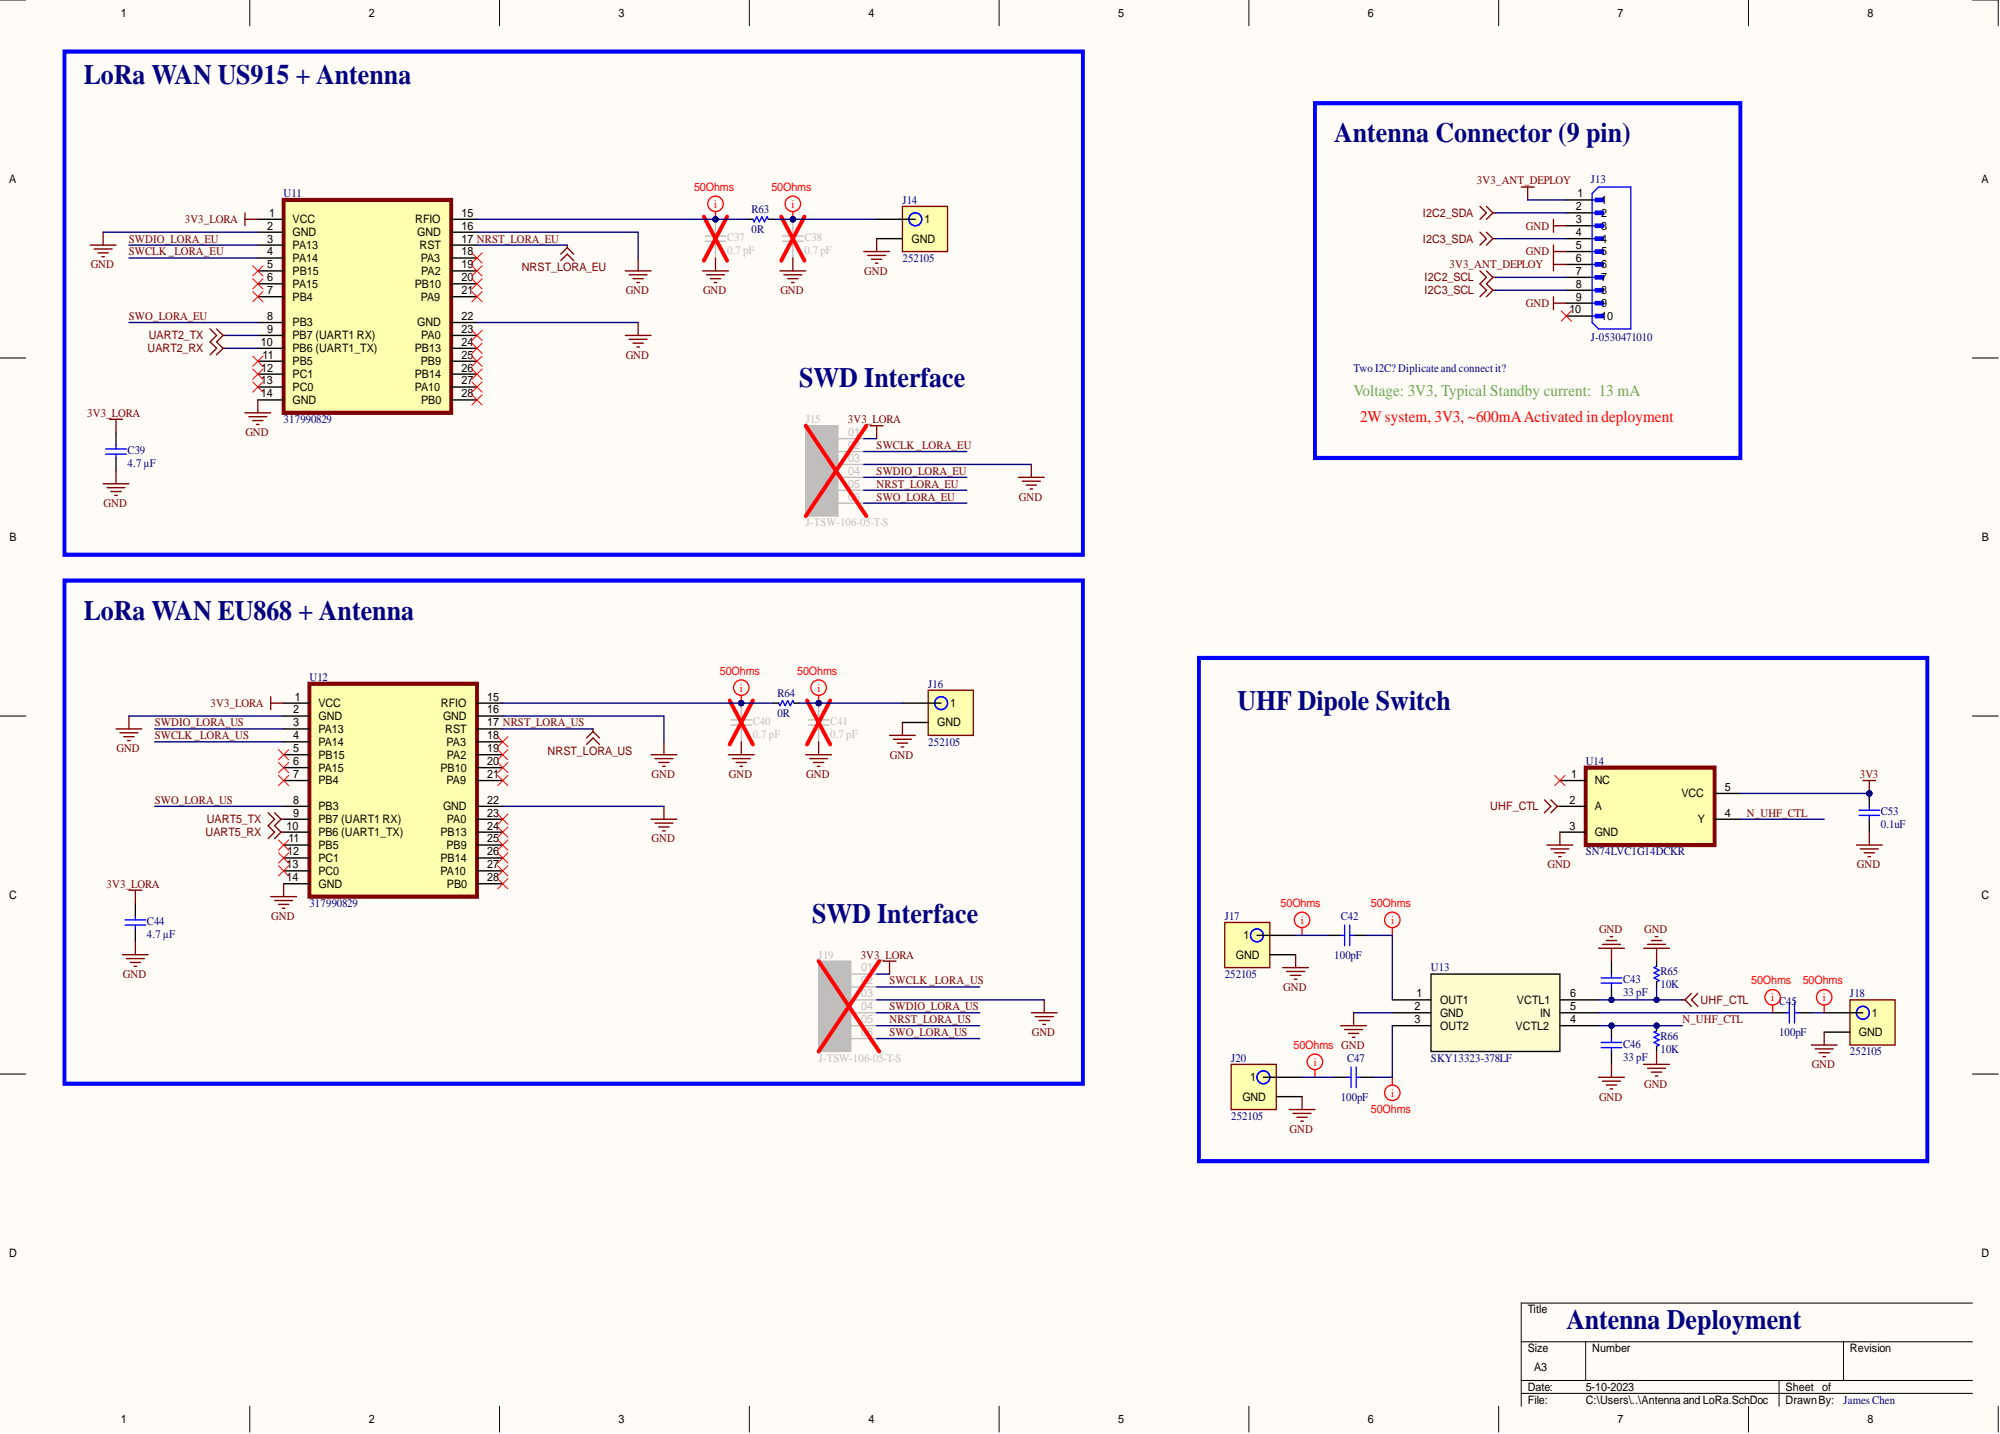
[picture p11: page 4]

Two I2C? Diplicate and connect it?
Voltage: 3V3, Typical Standby current: 13 mA
2W system, 3V3, ~600mA Activated in deployment

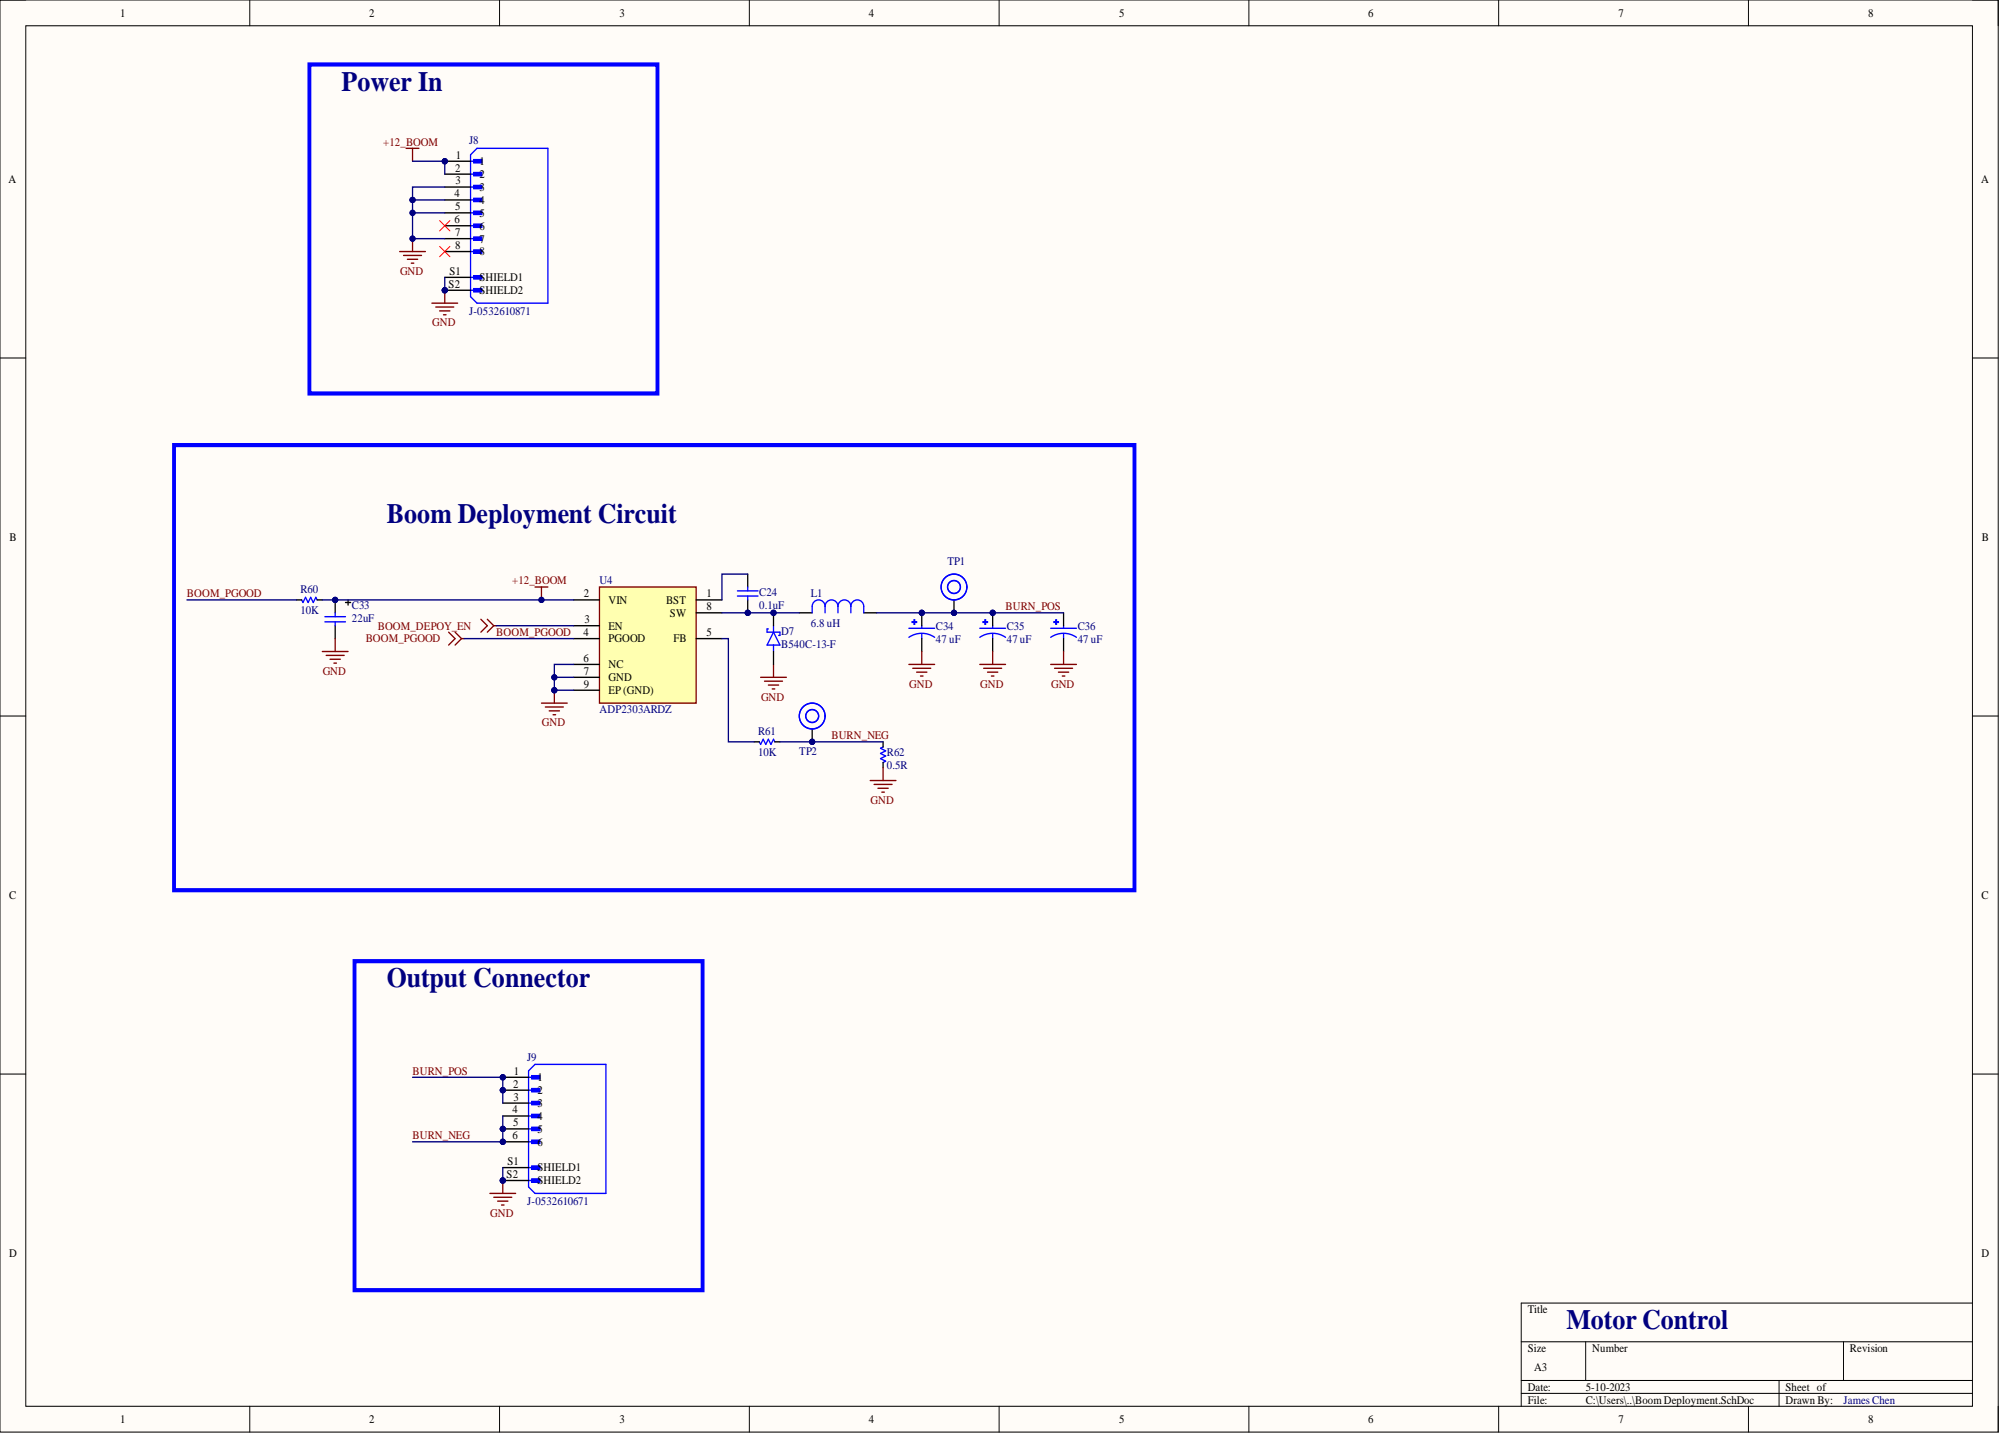
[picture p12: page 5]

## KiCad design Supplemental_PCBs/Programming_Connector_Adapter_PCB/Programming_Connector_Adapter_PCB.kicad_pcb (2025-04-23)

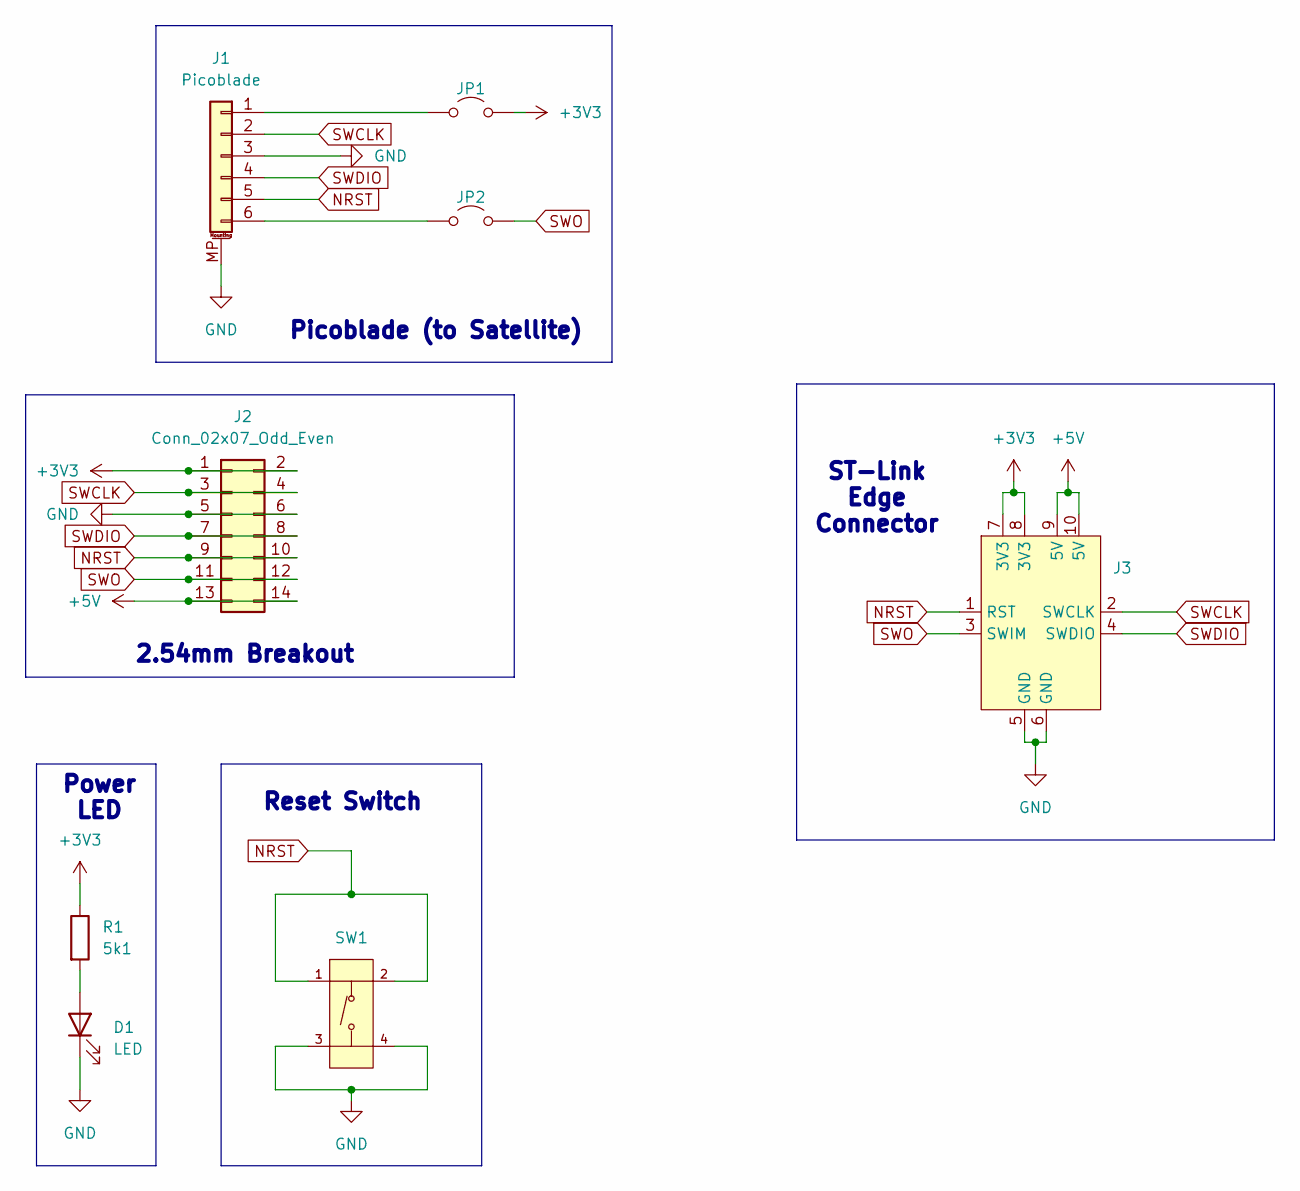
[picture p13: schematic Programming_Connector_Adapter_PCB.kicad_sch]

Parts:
D1: LED; LED_0603_1608Metric_Pad1.05x0.95mm_HandSolder
J1: Picoblade; Molex_PicoBlade_53261-0671_1x06-1MP_P1.25mm_Horizontal
J2: Conn_02x07_Odd_Even; PinHeaderSocket_2x07_P2.54mm_Vertical
J3: ST_Link_Edge_Connector
JP1, JP2: Jumper_2_Open; PinHeader_2x01_P2.54mm_Vertical
R1: 5k1; R_0603_1608Metric_Pad0.98x0.95mm_HandSolder
SW1: Tactile_Button,_160gf; SW-SMD_4P-L5.1-W5.1-P3.70-LS6.5-TL-2; Voltage Rating (Dc) 12V; Part TS-1187A-B-A-B; LCSC C318884

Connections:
+3V3: J2.1, J2.2, J3.7 (3V3), J3.8 (3V3), JP1.2 (B), R1.1
+5V: J2.13, J2.14, J3.9 (5V), J3.10 (5V)
GND: D1.1 (K), J1.3, J1.MP (MountPin), J2.5, J2.6, J3.5 (GND), J3.6 (GND), SW1.3 (C), SW1.4 (D)
NRST: J1.5, J2.9, J2.10, J3.1 (RST), SW1.1 (A), SW1.2 (B)
unnamed: D1.2 (A), R1.2
unnamed: J1.1, JP1.1 (A)
unnamed: J1.6, JP2.1 (A)
SWCLK: J1.2, J2.3, J2.4, J3.2 (SWCLK)
SWDIO: J1.4, J2.7, J2.8, J3.4 (SWDIO)
SWO: J2.11, J2.12, J3.3 (SWIM), JP2.2 (B)

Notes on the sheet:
2.54mm Breakout
Power LED
Reset Switch
ST-Link Edge Connector
Picoblade (to Satellite)

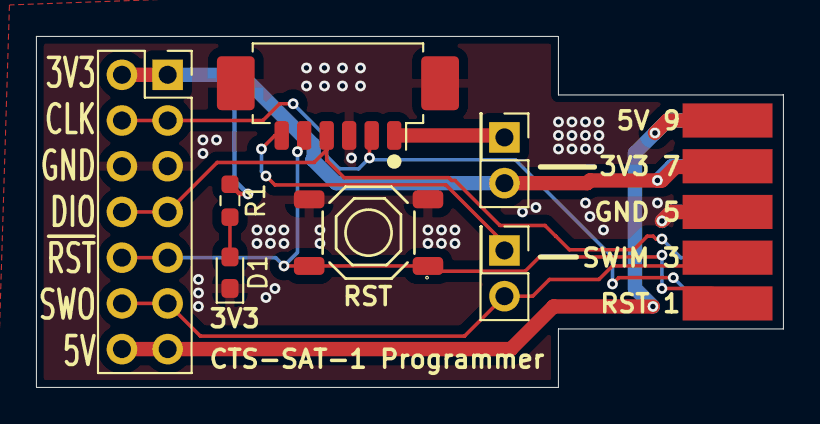
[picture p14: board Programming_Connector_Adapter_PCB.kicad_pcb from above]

Board: 2 copper layers, 41.5 x 19.5 mm, 8 parts (0 on the bottom side), 10 nets.

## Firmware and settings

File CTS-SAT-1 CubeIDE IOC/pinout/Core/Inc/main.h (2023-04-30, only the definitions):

#define GPLED1_Pin GPIO_PIN_2
#define GPLED1_GPIO_Port GPIOE
#define GPLED2_Pin GPIO_PIN_3
#define GPLED2_GPIO_Port GPIOE
#define GPLED3_Pin GPIO_PIN_4
#define GPLED3_GPIO_Port GPIOE
#define CAMERA_EN_Pin GPIO_PIN_2
#define CAMERA_EN_GPIO_Port GPIOA
#define GPS_PPS_Pin GPIO_PIN_6
#define GPS_PPS_GPIO_Port GPIOA
#define FLASH_NCS_A2_Pin GPIO_PIN_0
#define FLASH_NCS_A2_GPIO_Port GPIOG
#define FLASH_NCS_A1_Pin GPIO_PIN_1
#define FLASH_NCS_A1_GPIO_Port GPIOG
#define FLASH_CS_A0_Pin GPIO_PIN_7
#define FLASH_CS_A0_GPIO_Port GPIOE
#define FRAM_NCS_1_Pin GPIO_PIN_8
#define FRAM_NCS_1_GPIO_Port GPIOE
#define FRAM_NCS_0_Pin GPIO_PIN_9
#define FRAM_NCS_0_GPIO_Port GPIOE
#define MOTOR_NFAULT_Pin GPIO_PIN_12
#define MOTOR_NFAULT_GPIO_Port GPIOB
#define MOTOR_NEN_Pin GPIO_PIN_13
#define MOTOR_NEN_GPIO_Port GPIOB
#define MOTOR_PWM_Pin GPIO_PIN_14
#define MOTOR_PWM_GPIO_Port GPIOB
#define MOTOR_DIR_Pin GPIO_PIN_15
#define MOTOR_DIR_GPIO_Port GPIOB
#define ENCODER_EN_Pin GPIO_PIN_8
#define ENCODER_EN_GPIO_Port GPIOD
#define ENCODER_I_Pin GPIO_PIN_9
#define ENCODER_I_GPIO_Port GPIOD
#define ENCODER_B_Pin GPIO_PIN_10
#define ENCODER_B_GPIO_Port GPIOD
#define ENCODER_A_Pin GPIO_PIN_11
#define ENCODER_A_GPIO_Port GPIOD
#define MPI_RX_NEN_Pin GPIO_PIN_4
#define MPI_RX_NEN_GPIO_Port GPIOG
#define MPI_TX_EN_Pin GPIO_PIN_5
#define MPI_TX_EN_GPIO_Port GPIOG

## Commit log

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2021-08-08 added PC104 header labels, added load caps for oscillator
    [OBC_boardV1.SchLib, PC104_headers_and_storage.SchDoc, STM32.SchDoc]
2021-08-14 MPI RS422 schematic
    did RS422 with maxim transceiver, added level shifter for rx/tx enable lines. should update stm project with new pins
    [OBC_boardV1.SchLib, PC104_headers_and_storage.SchDoc, STM32.SchDoc]
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2021-10-30 add LDO, swap STM32 for 144pin
    [External Connectors.SchDoc, Memory.SchDoc, Microcontroller.SchDoc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]
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2021-12-15 added camera pinout, swap to stm32l4r5zi with dcmi
    [Camera.SchDoc, External Connectors.SchDoc, Memory.SchDoc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]
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2021-12-18 changed to 2mm pitch, need to check if correct
    [External Connectors.SchDoc, OBC Development Board.SchLib]
2021-12-19 Revert "debug"
    This reverts commit a9be2125b960059e23b02acd5c2186153c76f217.
    [OBC Development Board.PrjPcb]
2021-12-19 Revert "changed to 2mm pitch, need to check if correct"
    This reverts commit 68a31112bea4ffca7d86dd24d84ac09ad777736d.
    [External Connectors.SchDoc, OBC Development Board.SchLib]
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2022-01-07 rearrange controlled impedance traces, resolve design rule errors
    [External Connectors.SchDoc, Motor Control.SchDoc, OBC Development Board.SchLib]
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2022-05-12 minor changes, flip encoder net error
    [Motor Control.SchDoc, OBC Development Board.PrjPcb, OBC Development Board.SchLib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]
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2023-03-09 commit burn wire development board
    [Burn Wire Dev Board.GBL, Burn Wire Dev Board.GBO, Burn Wire Dev Board.GBP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]
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2023-04-18 more rev 1.2 schematic changes
    LoRaWAN Circuitry
    UHF dipole switch
    20 MHz TCXO
    32KHz TCXO
    Power Systems connections
    Boom deployment
    [Antenna and LoRa.SchDoc, Boom Deployment.SchDoc, External Connectors.SchDoc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]
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2023-05-01 rough component and connector layout
    layout most connector locations subject to change. and placed sensitive components
    [Antenna and LoRa.SchDoc, Boom Deployment.SchDoc, External Connectors.SchDoc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]
2023-05-03 finish first attempt at layout
    completed all connections, still need to resole some design rule errors
    [Antenna and LoRa.SchDoc, Boom Deployment.SchDoc, External Connectors.SchDoc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]
2023-05-08 resolve errors and generate design files
    [Antenna and LoRa.SchDoc, Bill of Materials-OBC Development Board(Build).xlsx, Boom Deployment.SchDoc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]
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2023-05-10 change debug uart pinout
    swap tx/rx on stm and umbilical
    [External Connectors.SchDoc, STM32.SchDoc]
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2023-08-30 Version3: Change R107 and R109 to 0 ohm resistors to stop distortion
    [STM32.SchDoc]
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2023-08-30 Version3: Flip TX and RX for USART1 for MPI
    [STM32.SchDoc]
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2023-09-16 Version3: Fix footprint silkscreens
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2023-09-16 Version3: As done as it can be without burnwire and rf switch testing
    [OBC Development Board.PrjPcb]
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2023-12-09 Version3: Fix labelling and check UART
    [Antenna and LoRa.SchDoc, External Connectors.SchDoc, STM32.SchDoc]
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2023-12-22 Version3: Update burnwire config
    [Boom Control.SchDoc]
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2024-02-28 Version3: Back to 307 errors :)
    [Antenna and LoRa.SchDoc]
2024-03-23 swapped debug UART and antenna B I2C
    Schematic: swap debug LPUART1 and I2C_3. Now:
    - PC0 = Ant B SCL (I2C_3)
    - PC1 = Ant B SDA (I2C_3)
    - PG8 = Debug UART MISO RX (LPUART1)
    - PG7 = Debug UART MOSI TX (LPUART1)
    [STM32.SchDoc]
2024-04-06 Rerouting and DRC fixes (#2)
    * made routing changes
    put resistor into place, and re-routed Nreset
    * Rerouted comms lines
    Rerouted Debug UART (92/93) and Antenna I2C B (26/27) lines. Attempted to clear some of the clearance constraints pointed our by DRC as well.
    * Cleared some DRC errors
    Updates footprint slikscreen for J-53261-0471 and cleared room(s) at bottom left of layout
    * Ran DRC
    Ran DRC and updated silk screen error
    * Cleared all Silk screen errors
    * Eliminated Net Antennae and Polygon Pour Errors
    Still need to address differential pairs and dead copper layers
    * Update OBC Development Board.PcbDoc
    * Ran DRC
    ---------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
    [Antenna and LoRa.SchDoc, STM32.SchDoc]
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2024-04-27 Resolved DRC regarding clearance
    - changed the pin 1 indicator that were causing the clearance error.
    -changed thickness of the differential pair routing from 10 mil to 5.8 mil. Now the only error left is the length of the differential pair
    - Dead solder DRC error, can be ignored and agreed by Parker
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2024-06-15 Edited Schematics
    Removed EU LoRa and used freed UART5 line for EPS. Created switch for UART2 lines connecting it to both the PC104 and the US LoRa.
    [Antenna and LoRa.SchDoc, External Connectors.SchDoc, STM32.SchDoc]
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2024-06-19 Made minor schematic and routing changes
    Switched CS lines on each Flash memory IC and made resulting routing changes. Rearranged components near the EPS pico-blade connector and modified traces to the connector to eliminate polygon shards in L3. *Note - need to reroute burnwire components to account for another high-current loop.
    [Antenna and LoRa.SchDoc, Boom Control.SchDoc, Memory.SchDoc]
2024-06-22 Cleared DRC Silkscreen Errors
    Silkscreen errors on R72 and R73 cleared. Note* that previous mentions of rerouting burnwire and boom deployment circuitry were scrapped after further research.
2024-07-03 Used latest OBC review to fix design errors
    Ensured stitching vias did not encroach into keep-out zones. Rerouted COMS to clear some space near RF portion of layout. Fixed name changes on schematic and title blocks.
    [Antenna and LoRa.SchDoc, Boom Control.SchDoc, External Connectors.SchDoc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]
2024-07-06 Went through with Review comments
    Adjusted position of resistor switches (R72-75), shortened I2C3 traces coming from STM, attempted to minimize stubs.
2024-07-09 Minimized umbillical connector
    Removed MPI UART and Memory SPI interfaces from umbilical connection and removed all unnecessary routes.
    [External Connectors.SchDoc]
2024-07-11 Placed new 47uF capacitors for boom deployment circuit, added Burn Wire Dev Board Library to project
    [Boom Control.SchDoc, OBC Development Board.PrjPcb]
2024-07-12 Placed new 47uF ceramic capacitors to replace the big aluminum capacitors
    Capacitors were chosen based on recommendations from the Buck Regulator Datasheet
    [Boom Control.SchDoc]
2024-07-12 Reorganized burnwire circuitry
    Replaced components for boom control circuitry, with emphasis placed on high current movement. U4, L1, R62, J8 and J9 identified as high current loop, and thus were placed in close proximity. Routing still needs to be done
    [Boom Control.SchDoc]
2024-07-12 (Almost) Fully routed burnwire circuitry
    Created polygons to cover high current loop (12V Boom on J8 into U4 Pin 2 --> U4 Pin 8 into L1 --> L1 to Burn Pos on J9 --> Burn Neg on J9 to R62 --> R62 to GND). Note that some polygons were automatically created with thermal reliefs vs others with solid fills (would prefer solid fills for all). Once final capacitor footprint is updated, routing will be complete.
2024-07-12 Switched 22/0 ohm resistors, added 0.1uF capacitor to NBOOT or Clock, Added footprints for ceramic capacitors for burnwire circuit
    [Boom Control.SchDoc, OBC Development Board.SchLib, STM32.SchDoc]
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2024-07-12 Changed C34 on burnwire circuit
    [Boom Control.SchDoc, STM32.SchDoc]
2024-07-12 Fixed Capacitor Error C34 on burnwire
    [Boom Control.SchDoc, OBC Development Board.SchLib, STM32.SchDoc]
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2024-07-12 Routed remaining components
    Routed remaining burnwire circuitry and extended corresponding polygons. Routed new 22 ohm resistors in place of 0 ohm resistors. Routed new boot cap.
2024-07-13 Adjusted thermal reliefs
    Adjusted thermal reliefs on burnwire circuitry to account for high current flow.
    [Boom Control.SchDoc]
2024-07-15 Replaced R33 with 0.33Ohm 4W resistor, added part to OBC Schematic Library
    [Boom Control.SchDoc, OBC Development Board.SchLib]
2024-07-15 Got rid of MFN label on schematic for R33 on boom circuit
    [Boom Control.SchDoc]
2024-07-16 Added MT29F16G08ABACAWP-AAT:C TR memory module, made its schematic, footprint, and step file, started creating pin/wire connections based on details from the datasheet
    [Memory.SchDoc, OBC Development Board.SchLib]
2024-07-18 Replaced 48 pin flash with new 16 pin MT29F1G01ABAFDSF-AAT:F TR
    [Memory.SchDoc, OBC Development Board.SchLib]
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2024-07-18 Made SPI_NCS_FLASH_6 and SPI_NCS_FLASH_7 on the STM32 Schematic "No Connection" (they are not needed for the new flash module replacements)
    [STM32.SchDoc]
2024-07-19 Rerouted burnwire circuitry with R33
    [STM32.SchDoc]
2024-07-19 Finished routing new memory modules.
    Note that some small silkscreen changes need to be made.
    [Memory.SchDoc]
2024-07-20 Cleared DRC errors related to random traces and silkscreen
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2024-07-21 Updated driver-side series resistor placement
    Moved some series resistors towards driving pins on the STM. Note that not all series resistors have been replaced, and many still need to be moved (and polygons need to be repoured).
    [STM32.SchDoc]
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2024-07-23 Connected series resistors to driver side MISO pins
    Added 22 ohm resistors (6 total) to each flash and fram module along the MISO lines and routed them.
    [Memory.SchDoc]
2024-07-27 Added a backup "remove before flight" connector
    Added picoblade connects along with 8 resistors to create a remove-before-flight connector. Two random GPIO pins were chosen on the STM, and were hooked up to the connecter. The connector was then al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
    [External Connectors.SchDoc, STM32.SchDoc]
2024-07-30 Added VBAT monitor
    Routed the VBAT signal from the stack header to the STM through a 11:1 resistor divider. Ensured that the pin chosen uses embedded ADC. Allows monitoring of VBAT through the STM
    [External Connectors.SchDoc, STM32.SchDoc]
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2024-08-06 Switched the 22uF, 10V rated capacitor on Boom Deployment to 25V rated, added the schematic component to library
    [Boom Control.SchDoc, Memory.SchDoc, OBC Development Board.SchLib]
2024-08-06 Added 22ohm terminating resistor to LOA_MOSI_UART2_TX, added 0ohm terminating resistor to LORA_MISO_UART2_RX
    [Antenna and LoRa.SchDoc, Memory.SchDoc]
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2024-08-07 Added 22ohm and 0ohm resistors to MISO and MOSI of MPI RX and TX
    [External Connectors.SchDoc]
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2024-08-07 I forgot to save before pushing - added 25V rated 22uF tantalum cap to Boom deployment circuit
    [Boom Control.SchDoc]
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2024-08-09 Reorganized burnwire circuitry
    After our previous design review, our burnwire circuitry was identified as a weak point due to the EMI risks associated with the current layout. Several high current loops were identified and components were rearranged correspondingly.
    [Boom Control.SchDoc]
2024-08-10 Rearranged pinout of MPI Power In connector
    The "MPI Power In" connector mates with J7 on the EPS - in order to make the connection easier to facilitate, the pinout of the MPI connector was rearranged to mirror the pinout of J7 (noting that I2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
    [Boom Control.SchDoc]
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2024-08-14 Attempted to create variants in order to remove TP and Mounting holes from BOM
    [Boom Control.SchDoc]
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2024-08-21 Made final layout changes to burnwire circuitry
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2024-10-12 Schematic update
    Added comments for current and power characteristics for Debugging LEDs (D1-6)
    [STM32.SchDoc]
2025-01-08 Naming convention changes
    Changed the naming convention used in the schematic for the Programming/SWD connectors
    [External Connectors.SchDoc, STM32.SchDoc]
2025-01-11 Updated Memory modules and corresponding footprints
    Updated schematic to use 4 NAND mem modules (ie, replacing 2 of the existing NOR mem modules). Resulted in the elimination of 2 NCS lines, making PF13 and PF14 on the STM32 as NCs. Also resulted in t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
    [Memory.SchDoc, STM32.SchDoc]
2025-01-11 Modified RBF connector
    Removed RBF2, resulting in the elimination of R78, R80 and R82. Also results in PB15 becoming a NC. Note that further modifications to the RBF connector are also needed.
    [External Connectors.SchDoc, STM32.SchDoc]
2025-01-11 Updated connectors on schematic
    Moved J2 to "External connector" sheet and removed J21. Changes still need to be made to the layout to reflect the removal of J21
    [External Connectors.SchDoc, STM32.SchDoc]
2025-01-14 Updated connectors on schematic and layout
    Changed J15 from a 4-pin connector to a 2-pin connector connected to RBF1 and GND. Resulted in the removal of R68. Updated layout after removal of J21 on the schematic.
    [External Connectors.SchDoc, OBC Development Board.SchLib]
2025-01-15 Deleted burnwire circuitry.
    Deleted all components related to the boom deployment system and replaced them with a 2-pin picoblade connector to connect the OBC to the detached burn wire circuitry.
    [Boom Control.SchDoc]
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2025-01-15 Added notation fixes
    Changed schematic comment for temperature to reflect the correct device address and added a note on current consumption. Added silkscreen to the board to define the purpose of J4 (MPI Power).
    [STM32.SchDoc]
2025-01-18 Updated Reset line on SWD connector
    Replaced 0R with 22R on reset line coming from the SWD picoblade connector in order to eliminate previously occurring contention problem.
    [External Connectors.SchDoc, STM32.SchDoc]
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2025-01-29 Fixed the NRST contention
    Added series resistor to RST button to fix contention issues.
    [External Connectors.SchDoc, STM32.SchDoc]
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2025-02-18 Removed LED and modified BW connector
    Removed Debugging LED from PB7 (pin 137). Modified picoblade connector for burnwire to be 4-wide instead of 2-side (using extra two pins for two extra grounds)
    [External Connectors.SchDoc, STM32.SchDoc]
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2025-03-01 Routed Spare UART connector
    Routed spare UART connector (J9) - replaced series resistor on all LEDs with 4.7k ohm resistors (originally 220 ohms)
    [STM32.SchDoc]
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2025-03-08 Several changes
    1. Fixed schematic title blocks
    2. Pulled down unused pins on RS422 transceiver and GPS connector to GND
    [Antenna and LoRa.SchDoc, External Connectors.SchDoc, Memory.SchDoc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]
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2025-03-08 Added 10k pull up resistors to WP on all flash modules
    Added 10k pull ups to WP pins on all flash modules to prevent floating metal. WP pins are active low
    [External Connectors.SchDoc]
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2025-03-19 Added PU resistors on RX lines of USART2 and LPUART1 lines
    Needs fixing - layout is unable to fully update from schematic changes
    [External Connectors.SchDoc, STM32.SchDoc]
2025-03-19 Updated stack header footprint
    Updated stack header footprint with correct pin designators and added it to the schametic/layout.
    [External Connectors.SchDoc, OBC Development Board.SchLib]
2025-03-19 Changed PD res from H1-P2 to H1-P3 (fixed accidental mistake)
    [External Connectors.SchDoc]
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

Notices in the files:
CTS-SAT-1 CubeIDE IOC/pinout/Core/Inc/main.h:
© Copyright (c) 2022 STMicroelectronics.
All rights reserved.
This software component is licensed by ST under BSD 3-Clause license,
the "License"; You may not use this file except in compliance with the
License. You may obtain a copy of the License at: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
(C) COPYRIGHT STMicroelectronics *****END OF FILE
